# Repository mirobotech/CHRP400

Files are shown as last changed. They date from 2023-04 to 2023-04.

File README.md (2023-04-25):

# CHRP4

CHRP4 (Common Hardware Robotics Project 4, rev. 0) KiCad schematic and PCB design files.

Z30_0411

CHRP4 is a simple, versatile, and inexpensive microcontroller development system designed to help anyone make simple line-following, obstacle-sensing, or Sumo robots! CHRP4 is a robot-focused derivative of [UBMP4](https://mirobo.tech/chrp4), and was designed for learning or teaching PICmicro programming for robotic applications using either Microchip’s MPLAB X IDE or the cloud-based MPLAB Xpress IDE.

CHRP4 uses the [USB µC bootloader](https://hackaday.io/project/63204-usb-c-usb-pic-bootloader), which allows CHRP4 to appear as a mass storage drive for ease of programming. Simply drag and drop a compiled .hex file onto the ***PIC16F1459*** drive that shows up in your computer's device manager, and your program will start to run as soon as the file is transferred. The bootloader makes it possible to program CHRP4 using almost any kind of device, even enabling schools with 1:1 Chromebook programs to teach real C language microcontroller programming with Github integration.

The CHRP4 circuit board has a variety of simple I/O devices built-in so beginners can learn to code and make an assortment of different projects using just the parts on CHRP4 – no breadboarding, shields, or other modules are required. The on-board components allow CHRP4 to be built in a variety of configurations including: a minimal parts, education-focused trainer for specifically for teaching or learning microcontroller programming, a simple line-following robot, and, with the addition of an ultrasonic distance sensor module, an obstacle-sensing or Sumo robot.

## CHRP4 Hardware Features

- Microchip PIC16F1459 USB-capable microcontroller with 8k words of program FLASH (6k words free when using the USB bootloader), 128B of user FLASH, 1kB of RAM, 10-bit ADC, and a built-in temperature sensor
- optional SN754410 (or L293D) quad half-H bridge motor driver to run two DC motors in forward and reverse
- optional LF50AB low drop-out regulator for 6-12V battery operation
- 5 built-in pushbuttons
- 5 visible light LEDs
- 1 piezo beeper output
- optional 4-pin header for PORTC I/O pin expansion (designed for an HC-SR04 ultrasonic SONAR module, but can also connect to servos, optical sensors, NeoPixels, etc.)
- optional IR LED and phototransistor circuits integrated on three mini, break-away modules (one designed for line following robots, two designed for general floor sensing)
- optional IR demodulator for remote control decoding
- USB 2.0 type-C port for power and programming
- 6-pin ICSP (In-Circuit Serial Programming) header for PICkit-4

Find out more at [mirobo.tech/chrp4 ](https://mirobo.tech/chrp4), and see the CHRP4 description on [Hackaday](https://hackaday.io/project/190407-chrp4-usb-robotics-development-board).

## CHRP4 is Open

CHRP4 is open hardware and uses open source software – we want educators to have full access to the circuit, lesson materials, and code. The following permissions and conditions apply to CHRP4:
- the KiCad CHRP4 files stored in GitHub are open hardware licensed under the terms of the MIT license (except the mirobo.tech logo - see below). You are free to use and modify the CHRP4 files to make your own CHRP4 circuit boards.
- CHRP4 programs stored in GitHub are open source software licensed under the terms of the MIT license.
- CHRP4 learning materials on the mirobo.tech website are licensed under the terms of the Creative Commons CC-BY 4.0 license.
- the USB uC bootloader is open source and licensed under the terms of the GPL3.0 license by John Izzard.
- the mirobo.tech logo mark is a trademark of mirobo Technolgy and may not be used without prior permission.

## Can I buy a CHRP4?

CHRP4 boards, and kits are available at [mirobo.tech](https://mirobo.tech/chrp4).  
Bare CHRP4 printed circuit boards are also available from [OSHPARK](https://oshpark.com/shared_projects/rMynSTCb).

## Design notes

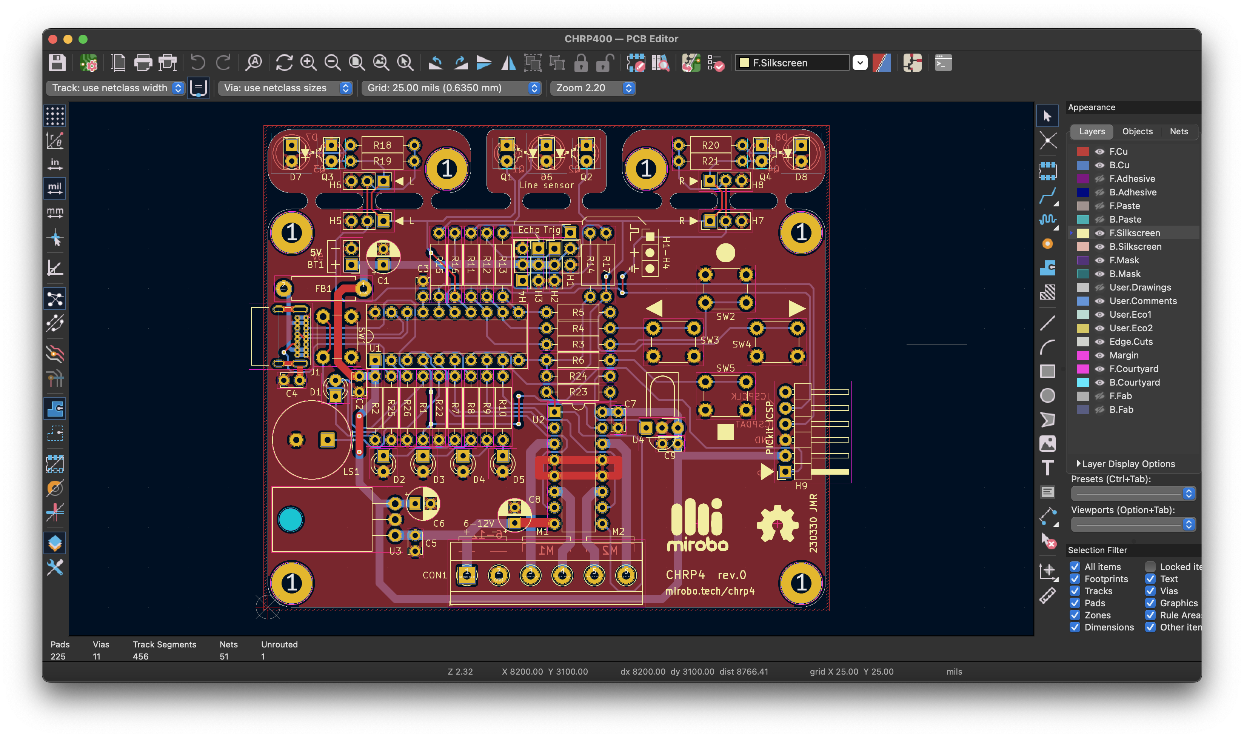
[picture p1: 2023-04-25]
Screen Shot 2023-04-04 at 1.32.04 PM.png

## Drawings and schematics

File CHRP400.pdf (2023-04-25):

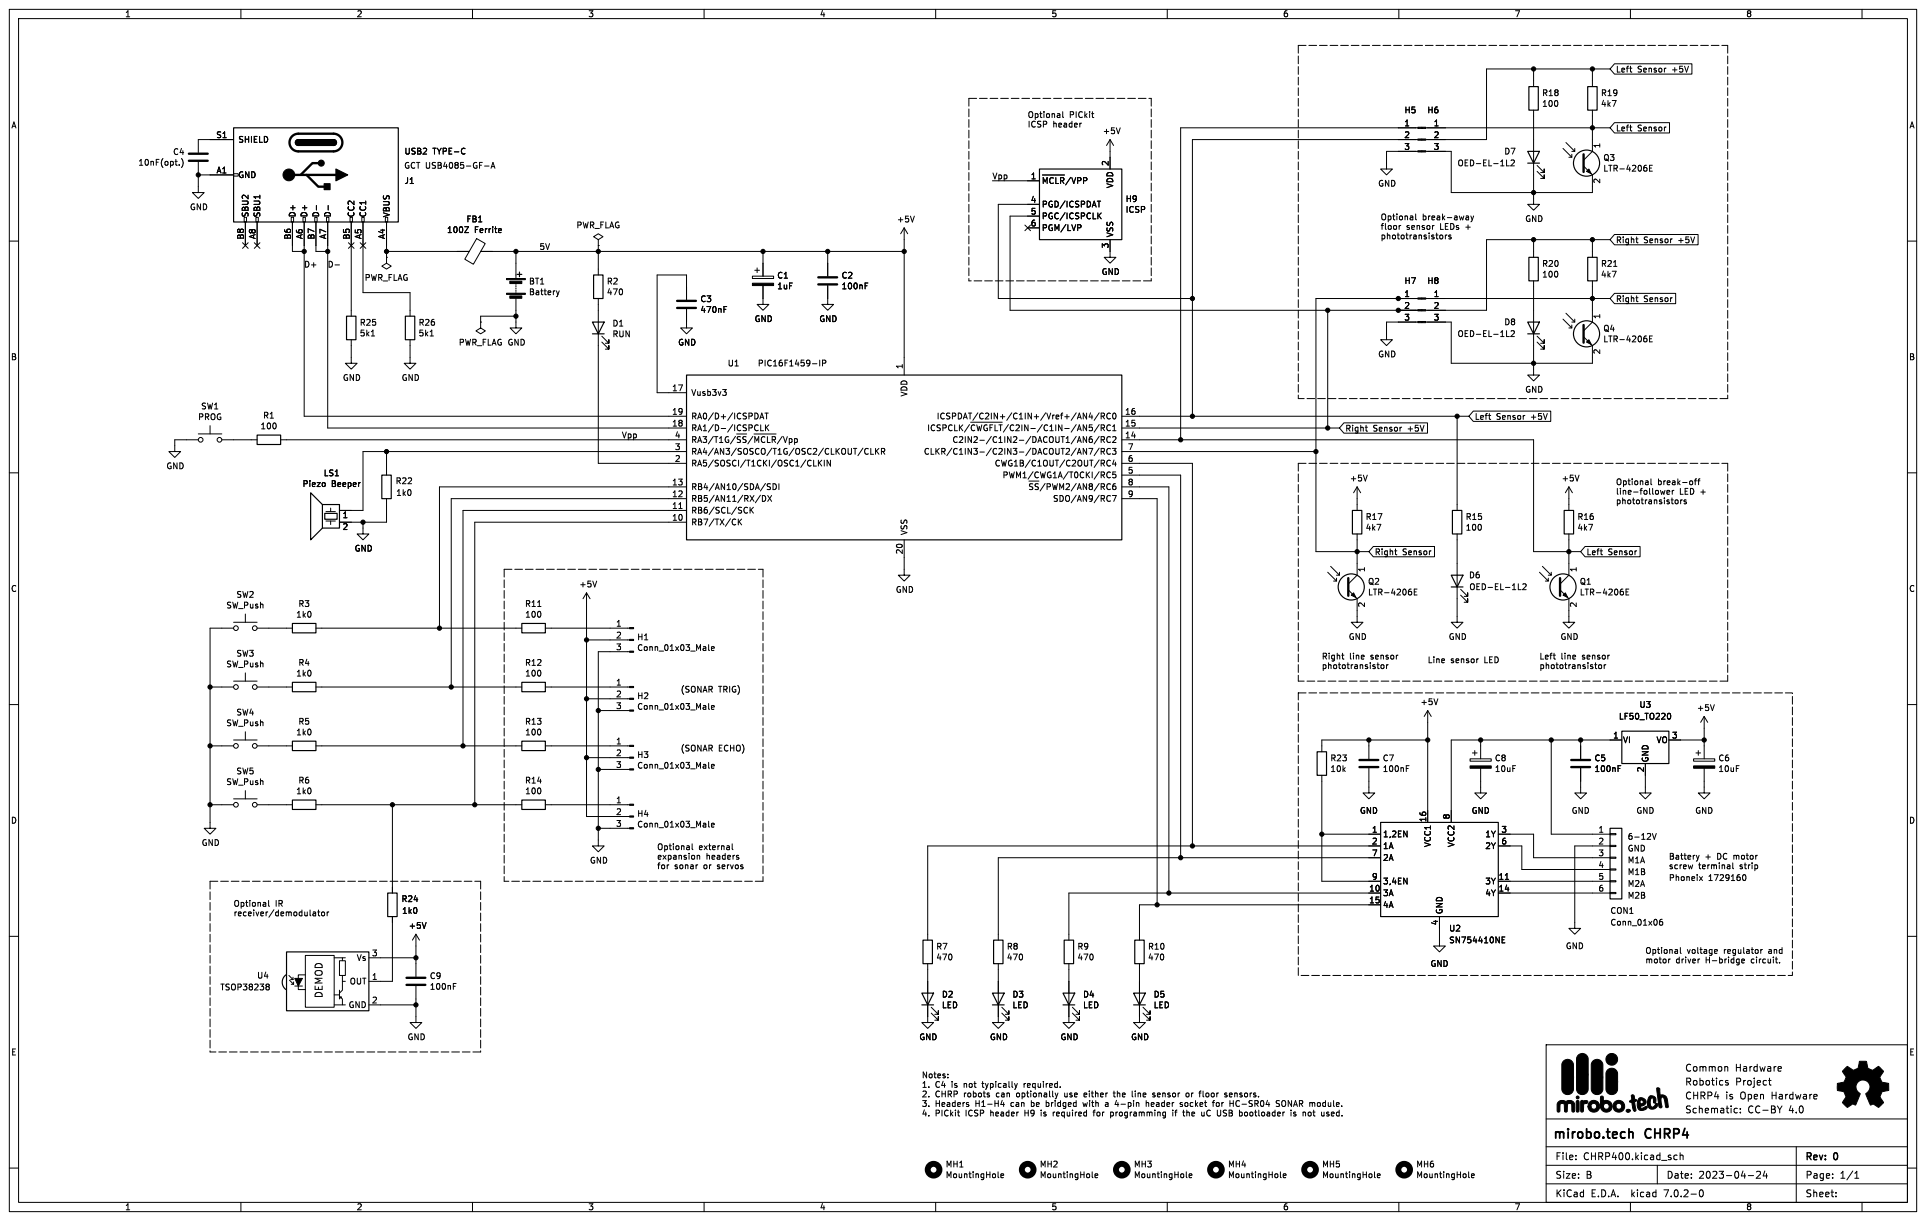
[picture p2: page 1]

Right Sensor Left Sensor +5V

3 PGD/ICSPDAT 4 PGC/ICSPCLK 5 PGM/LVP 6 H6

Left Sensor Right Sensor +5V

3 PGD/ICSPDAT 4 PGC/ICSPCLK 5 PGM/LVP 6 H9

1 RB7/TX/CK 10 RB6/SCL/SCK 11 RB5/AN11/RX/DX 12 RB4/AN10/SDA/SDI 13 C2IN2-/C1IN2-/DACOUT1/AN6/RC2 14 ICSPCLK/~{CWGFLT}/C2IN-/C1IN-/AN5/RC1

Phoneix 1729160 Right line sensor phototransistor

for sonar or servos

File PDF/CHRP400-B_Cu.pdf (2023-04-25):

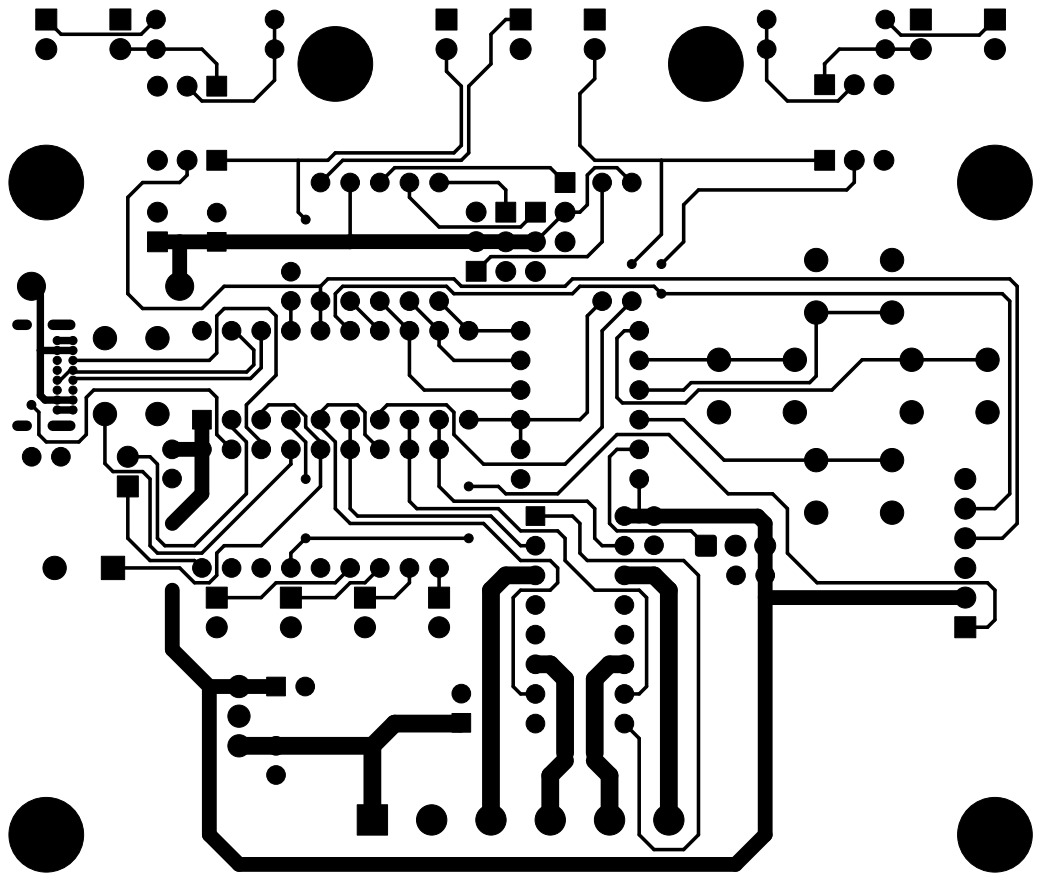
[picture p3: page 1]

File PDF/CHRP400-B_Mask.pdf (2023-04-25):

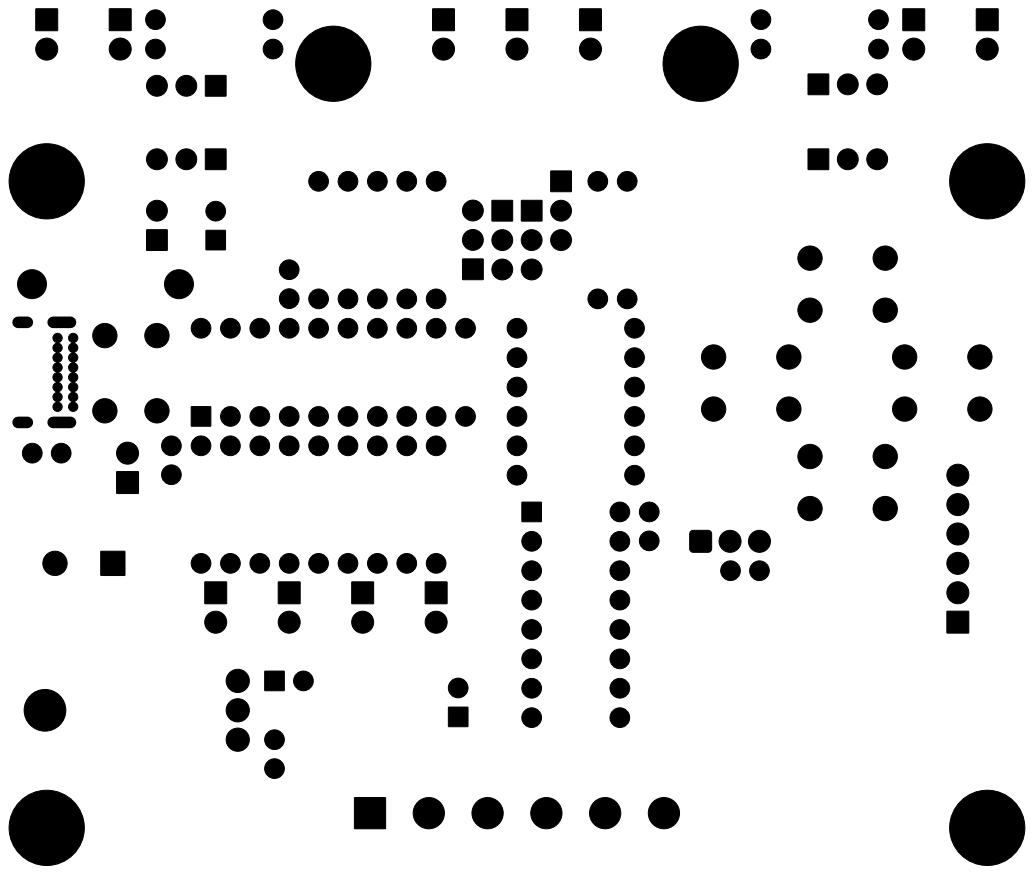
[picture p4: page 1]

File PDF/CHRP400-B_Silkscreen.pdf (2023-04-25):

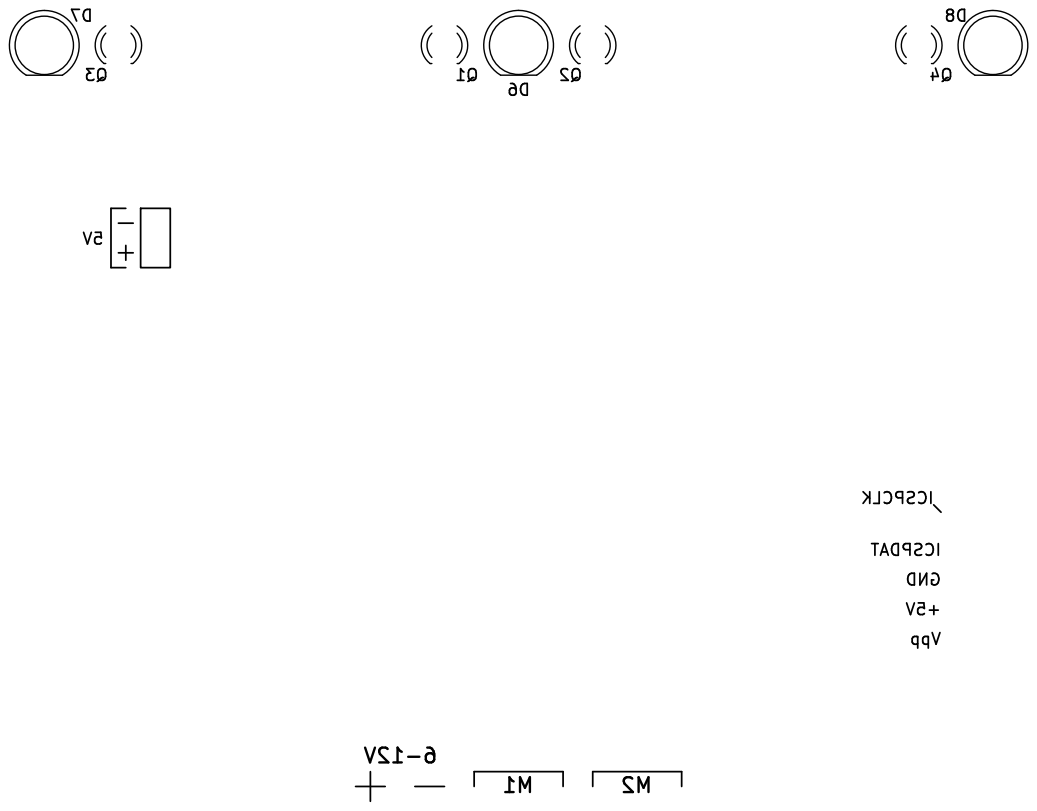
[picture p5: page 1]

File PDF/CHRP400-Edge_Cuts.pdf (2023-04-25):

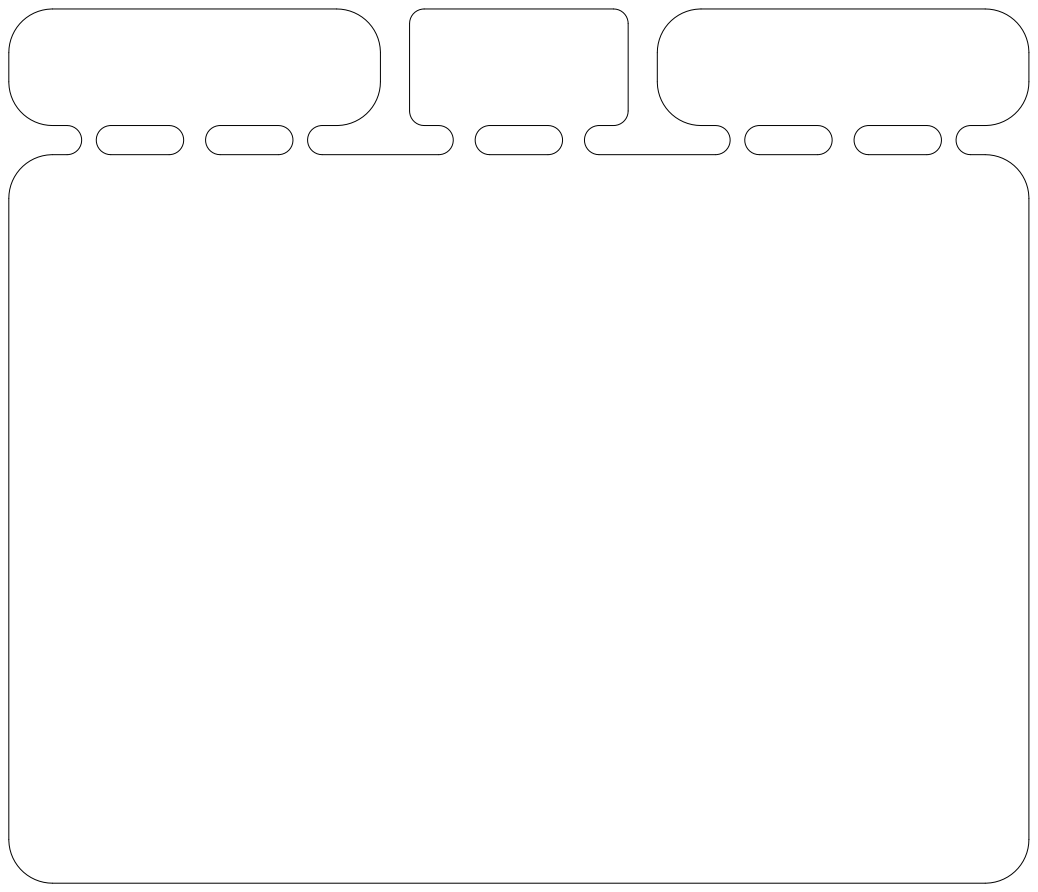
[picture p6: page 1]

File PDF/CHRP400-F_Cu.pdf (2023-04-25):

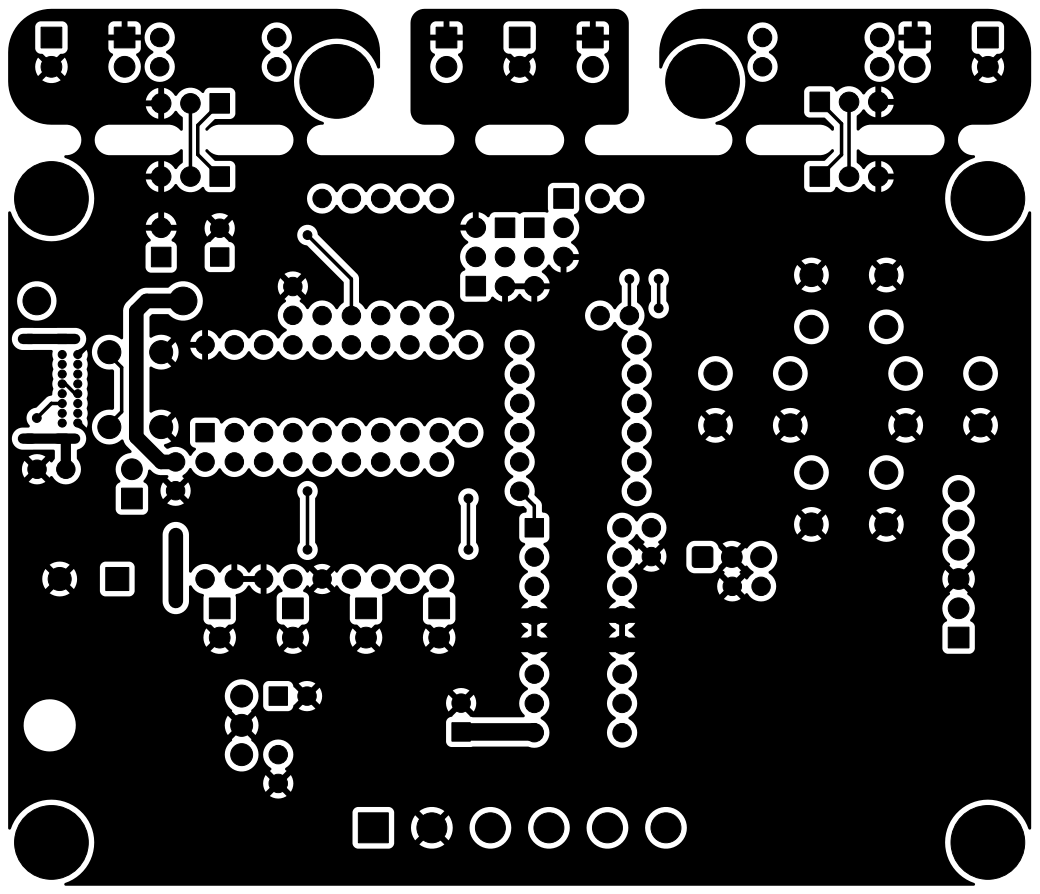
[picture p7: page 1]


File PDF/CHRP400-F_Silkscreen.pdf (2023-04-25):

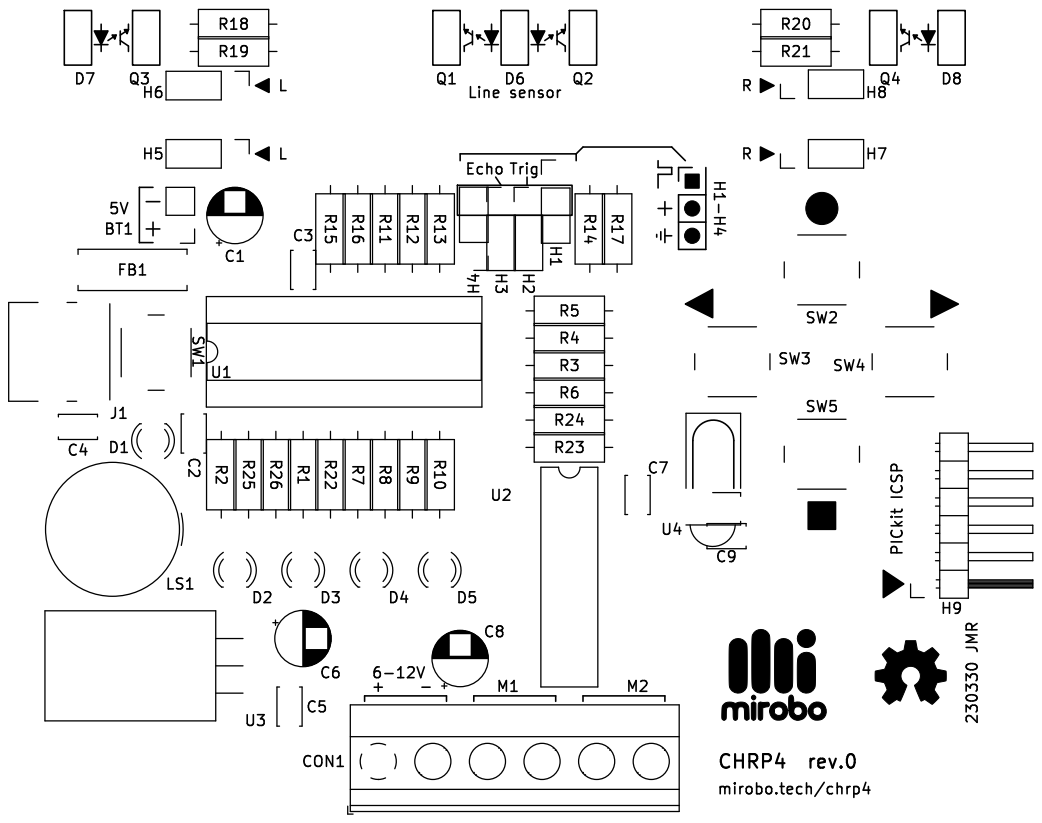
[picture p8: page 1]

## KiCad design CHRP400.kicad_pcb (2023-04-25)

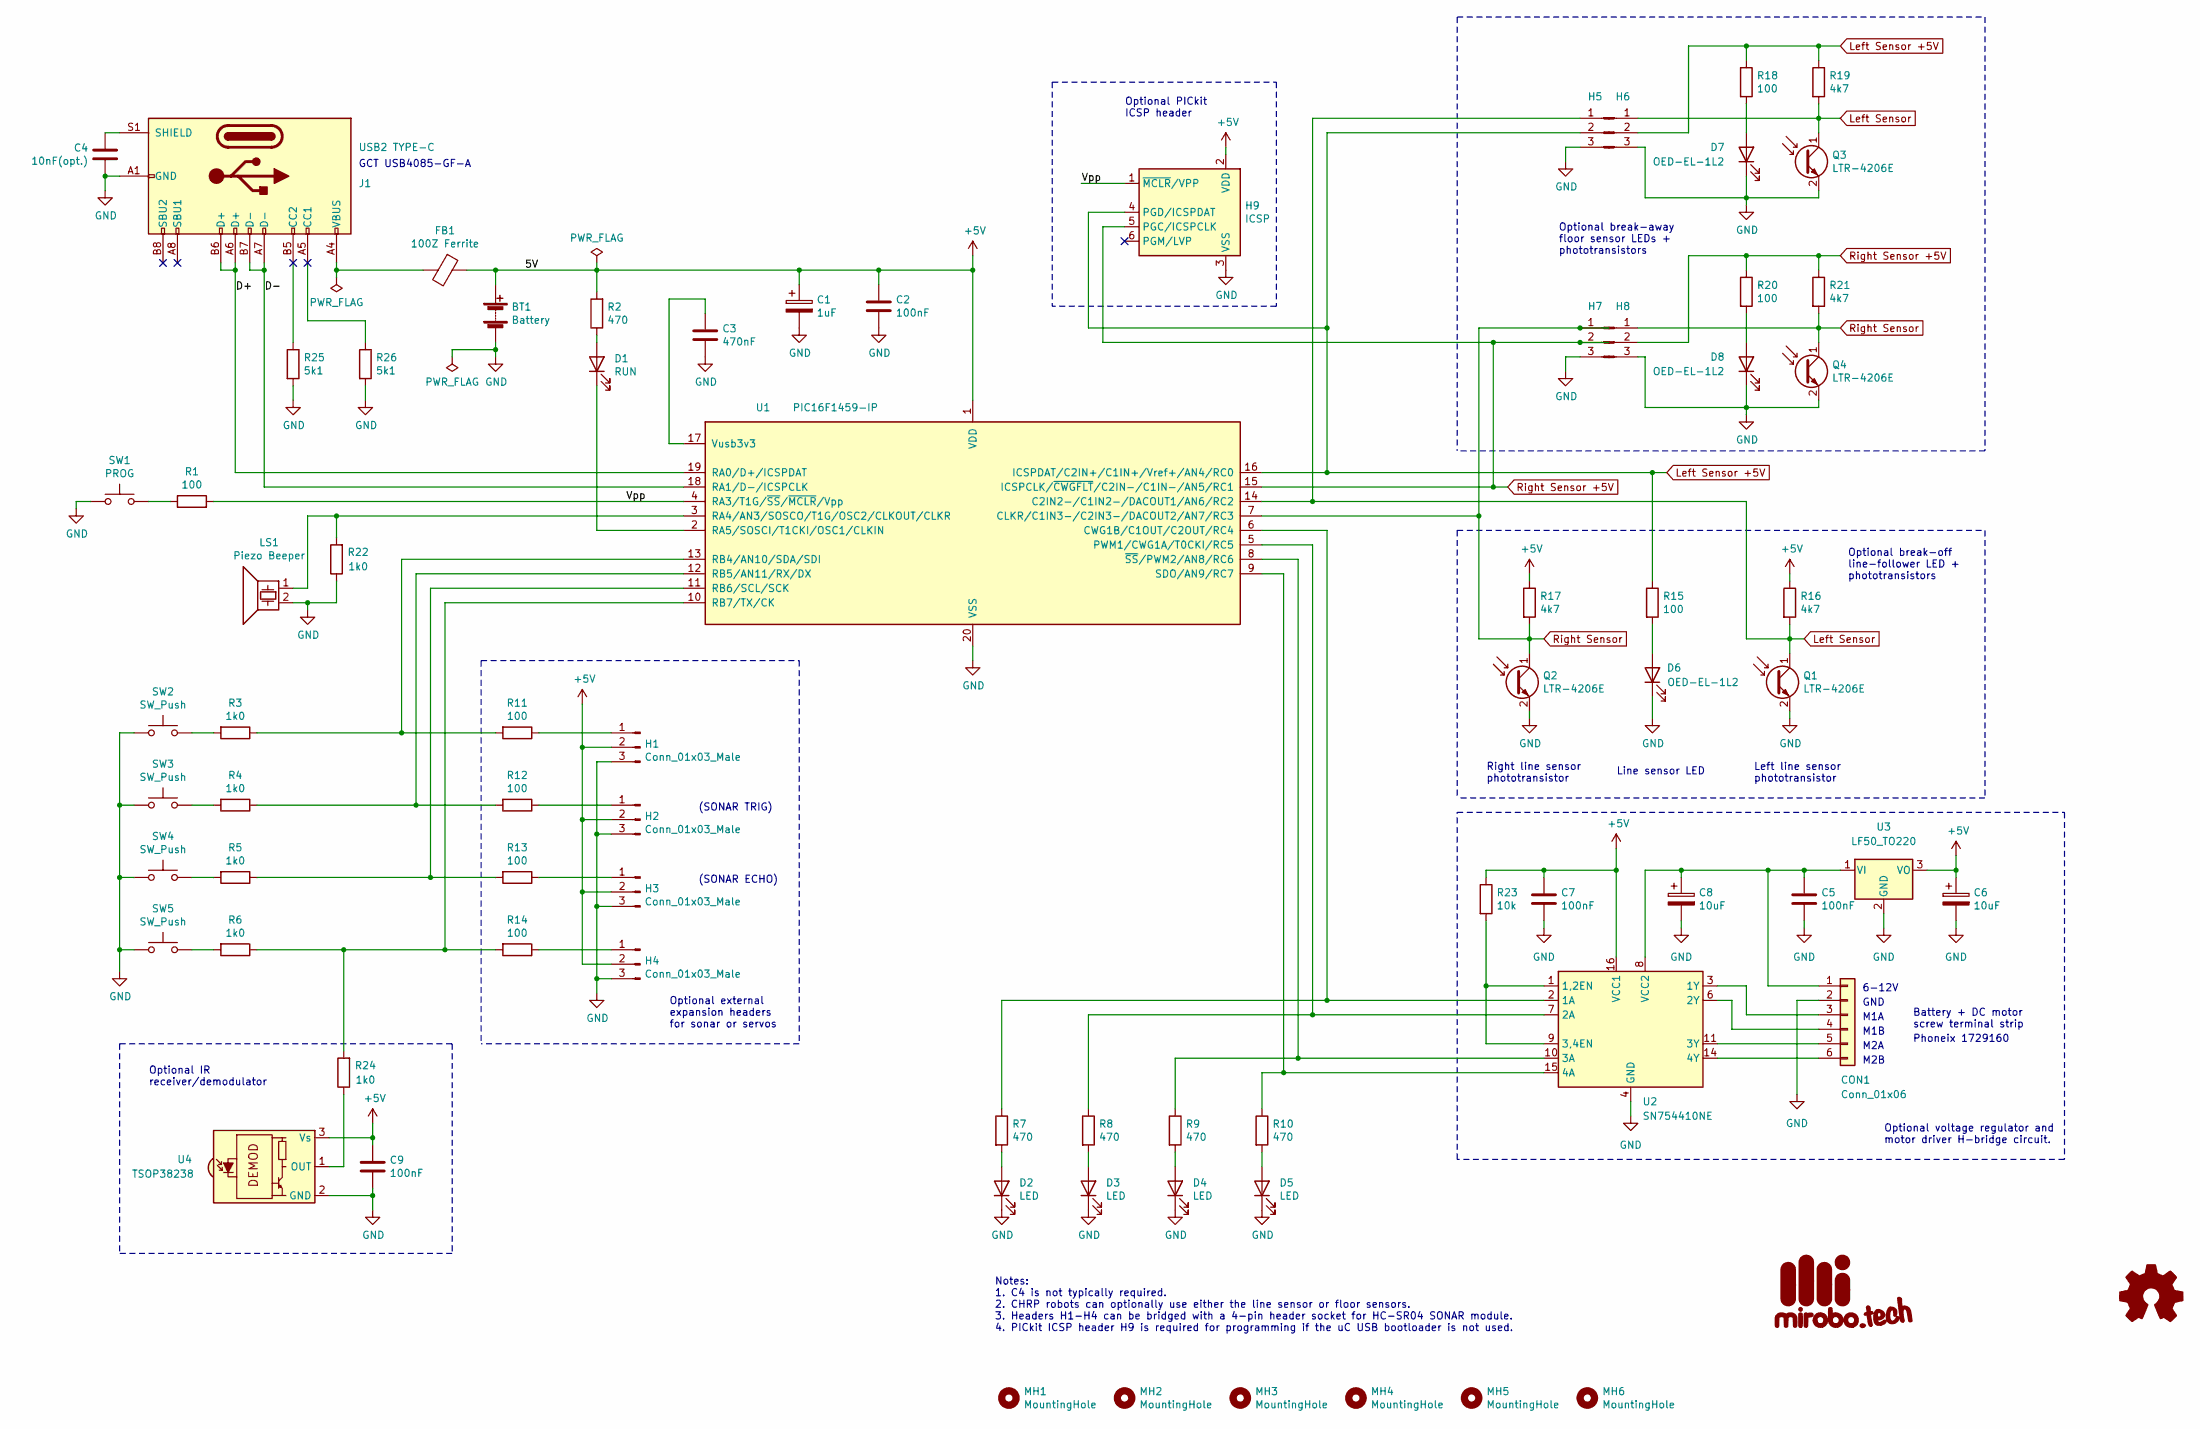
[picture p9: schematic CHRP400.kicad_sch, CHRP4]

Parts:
BT1: Battery; PinHeader_1x02_P2.54mm_Vertical
C1: 1uF; CP_Radial_D5.0mm_P2.50mm
C2, C5, C7, C9: 100nF; C_Disc_D3.4mm_W2.1mm_P2.50mm
C3: 470nF; C_Disc_D3.4mm_W2.1mm_P2.50mm
C4: 10nF(opt.); C_Disc_D3.4mm_W2.1mm_P2.50mm
C6, C8: 10uF; CP_Radial_D5.0mm_P2.50mm
CON1: Conn_01x06; TerminalBlock_Phoenix_MKDS-1,5-6-5.08_1x06_P5.08mm_Horizont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
D1: RUN; LED_D3.0mm
D2, D3, D4, D5: LED; LED_D3.0mm
D6, D7, D8: OED-EL-1L2; LED_D5.0mm_Clear
FB1: 100Z Ferrite; R_Axial_DIN0411_L9.9mm_D3.6mm_P12.70mm_Horizontal
G1: mirobotech_logo; mirobo_logo_10
G2: Logo_Open_Hardware_Small; OSHW-Symbol_6.7x6mm_SilkScreen
H1, H2, H3, H4, H5, H6, H7, H8: Conn_01x03_Male; PinHeader_1x03_P2.54mm_Vertical
H9: ICSP; PinHeader_1x06_P2.54mm_Horizontal
J1: USB2 TYPE-C; USB_C_Receptacle_GCT_USB4085
LS1: Piezo Beeper; Buzzer_TDK_PS1240P02BT_D12.2mm_H6.5mm
MH1, MH2, MH3, MH4, MH5, MH6: MountingHole; MountingHole_3.2mm_M3_Pad
Q1, Q2, Q3, Q4: LTR-4206E; LED_D3.0mm_IRBlack
R1, R11, R12, R13, R14, R15, R18, R20: 100; R_Axial_DIN0207_L6.3mm_D2.5mm_P10.16mm_Horizontal
R2, R7, R8, R9, R10: 470; R_Axial_DIN0207_L6.3mm_D2.5mm_P10.16mm_Horizontal
R3, R4, R5, R6, R22, R24: 1k0; R_Axial_DIN0207_L6.3mm_D2.5mm_P10.16mm_Horizontal
R16, R17, R19, R21: 4k7; R_Axial_DIN0207_L6.3mm_D2.5mm_P10.16mm_Horizontal
R23: 10k; R_Axial_DIN0207_L6.3mm_D2.5mm_P10.16mm_Horizontal
R25, R26: 5k1; R_Axial_DIN0207_L6.3mm_D2.5mm_P10.16mm_Horizontal
SW1: PROG; SW_PUSH_6mm
SW2, SW3, SW4, SW5: SW_Push; SW_PUSH_6mm
U1: PIC16F1459-IP; DIP-20_W7.62mm_Socket
U2: SN754410NE; DIP-16_W7.62mm
U3: LF50_TO220; TO-220-3_Horizontal_TabDown
U4: TSOP38238; Vishay_MINICAST-3Pin

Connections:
+5V: BT1.1 (+), C1.1, C2.1, C6.1, C7.1, C9.1, FB1.1, H1.2, H2.2, H3.2, H4.2, H9.2 (VDD), R2.2, R16.1, R17.1, R23.1, U1.1 (VDD), U2.16 (VCC1), U3.3 (VO), U4.3 (Vs)
/D+: J1.A6 (D+), J1.B6 (D+), U1.19 (RA0/D+/ICSPDAT)
/D-: J1.A7 (D-), J1.B7 (D-), U1.18 (RA1/D-/ICSPCLK)
/Vpp: H9.1 (~MCLR/VPP), R1.2, U1.4 (RA3/T1G/~SS/~MCLR/Vpp)
GND: BT1.2 (-), C1.2, C2.2, C3.2, C4.1, C5.2, C6.2, C7.2, C8.2, C9.2, CON1.2, D2.1 (K), D3.1 (K), D4.1 (K), D5.1 (K), D6.1 (K), D7.1 (K), D8.1 (K), H1.3, H2.3, H3.3, H4.3, H5.3, H6.3, H7.3, H8.3, H9.3 (VSS), J1.A1 (GND), J1.A12 (GND), J1.B1 (GND), J1.B12 (GND), LS1.2, Q1.2 (E), Q2.2 (E), Q3.2 (E), Q4.2 (E), R22.1, R25.2, R26.2, SW1.1, SW2.1, SW3.1, SW4.1, SW5.1, U1.20 (VSS), U2.4 (GND), U2.5 (GND), U2.12 (GND), U2.13 (GND), U3.2 (GND), U4.2 (GND)
Left Sensor: H5.1, H6.1, Q1.1 (C), Q3.1 (C), R16.2, R19.2, U1.14 (C2IN2-/C1IN2-/DACOUT1/AN6/RC2)
Left Sensor +5V: H5.2, H6.2, H9.4 (PGD/ICSPDAT), R15.1, R18.1, R19.1, U1.16 (ICSPDAT/C2IN+/C1IN+/Vref+/AN4/RC0)
unnamed: FB1.2, J1.A4 (VBUS), J1.A9 (VBUS), J1.B4 (VBUS), J1.B9 (VBUS)
unnamed: C5.1, C8.1, CON1.1, U2.8 (VCC2), U3.1 (VI)
unnamed: CON1.3, U2.3 (1Y)
unnamed: CON1.4, U2.6 (2Y)
unnamed: CON1.5, U2.11 (3Y)
unnamed: CON1.6, U2.14 (4Y)
unnamed: D1.2 (A), R2.1
unnamed: D1.1 (K), U1.2 (RA5/SOSCI/T1CKI/OSC1/CLKIN)
unnamed: D2.2 (A), R7.2
unnamed: D3.2 (A), R8.2
unnamed: D4.2 (A), R9.2
unnamed: D5.2 (A), R10.2
unnamed: D6.2 (A), R15.2
unnamed: D7.2 (A), R18.2
unnamed: D8.2 (A), R20.2
unnamed: H1.1, R11.1
unnamed: H2.1, R12.1
unnamed: H3.1, R13.1
unnamed: H4.1, R14.1
unnamed: C4.2, J1.S1 (SHIELD)
unnamed: R1.1, SW1.2
unnamed: R3.2, SW2.2
unnamed: R4.2, SW3.2
unnamed: R5.2, SW4.2
unnamed: R6.2, SW5.2
unnamed: R7.1, U1.6 (CWG1B/C1OUT/C2OUT/RC4), U2.2 (1A)
unnamed: R8.1, U1.5 (PWM1/CWG1A/T0CKI/RC5), U2.7 (2A)
unnamed: LS1.1, R22.2, U1.3 (RA4/AN3/SOSCO/T1G/OSC2/CLKOUT/CLKR)
unnamed: R3.1, R11.2, U1.13 (RB4/AN10/SDA/SDI)
unnamed: R4.1, R12.2, U1.12 (RB5/AN11/RX/DX)
unnamed: R5.1, R13.2, U1.11 (RB6/SCL/SCK)
unnamed: R6.1, R14.2, R24.2, U1.10 (RB7/TX/CK)
unnamed: R10.1, U1.9 (SDO/AN9/RC7), U2.15 (4A)
unnamed: C3.1, U1.17 (Vusb3v3)
unnamed: R9.1, U1.8 (~SS/PWM2/AN8/RC6), U2.10 (3A)
unnamed: R23.2, U2.1 (1,2EN), U2.9 (3,4EN)
unnamed: R24.1, U4.1 (OUT)
Right Sensor: H7.1, H8.1, Q2.1 (C), Q4.1 (C), R17.2, R21.2, U1.7 (CLKR/C1IN3-/C2IN3-/DACOUT2/AN7/RC3)
Right Sensor +5V: H7.2, H8.2, H9.5 (PGC/ICSPCLK), R20.1, R21.1, U1.15 (ICSPCLK/~CWGFLT/C2IN-/C1IN-/AN5/RC1)

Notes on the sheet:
M1A
M2B
Phoneix 1729160
(SONAR TRIG)
Line sensor LED
Left line sensor phototransistor
Notes: 1. C4 is not typically required. 2. CHRP robots can optionally use either the line sensor or floor sensors. 3. Headers H1-H4 can be bridged with a 4-pin header socket for HC-SR04 SONAR module. 4. PICkit ICSP header H9 is required for programming if the uC USB bootloader is not used.
GCT USB4085-GF-A
Optional break-off line-follower LED + phototransistors
Optional external expansion headers for sonar or servos
M1B
Optional break-away floor sensor LEDs + phototransistors
GND
Right line sensor phototransistor
(SONAR ECHO)
Optional voltage regulator and motor driver H-bridge circuit.
Optional IR receiver/demodulator
M2A
Battery + DC motor screw terminal strip
6-12V
Optional PICkit ICSP header

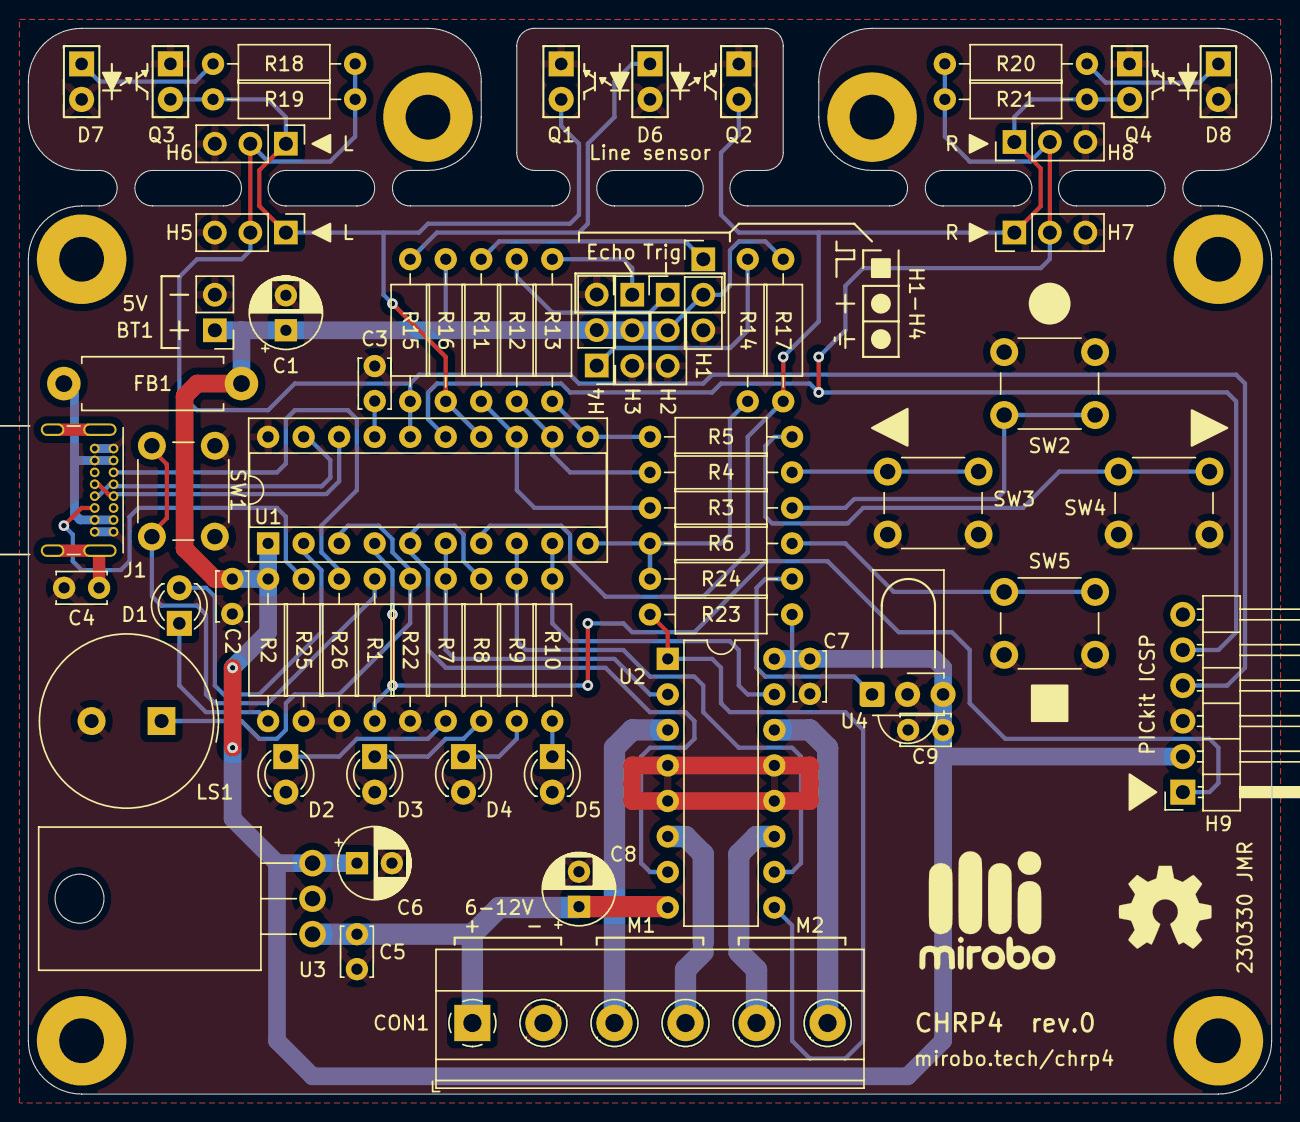
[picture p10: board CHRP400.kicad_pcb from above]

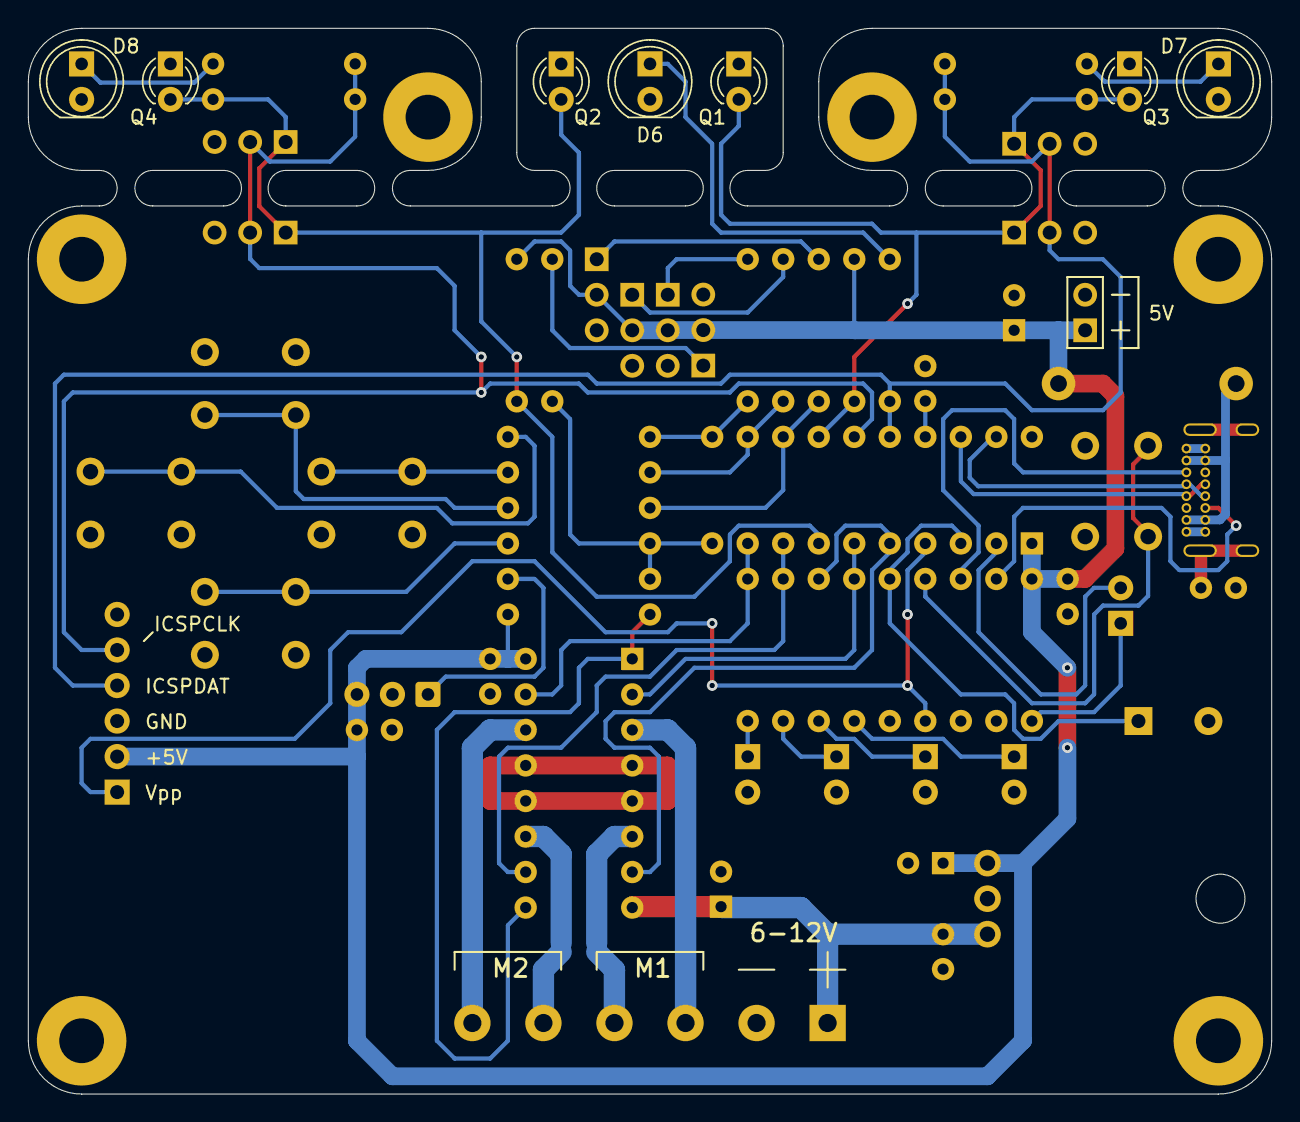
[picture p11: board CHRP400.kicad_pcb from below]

Board: 2 copper layers, 88.9 x 76.2 mm, 78 parts (7 on the bottom side), 46 nets.

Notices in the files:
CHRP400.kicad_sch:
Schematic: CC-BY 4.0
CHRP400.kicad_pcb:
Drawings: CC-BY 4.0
